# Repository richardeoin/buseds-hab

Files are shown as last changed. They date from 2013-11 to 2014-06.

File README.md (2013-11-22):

TODO: Find a better name for this project than "buseds-hab"!

### [Components List](Components.md)

### [Block Diagram](Block-Diagram.md)

### [Power Budget](power-budget.md)

### Design Notes

The electronics collects data from the sensors and GPS. [Common GPS errors](http://ukhas.org.uk/guides:common_coding_errors_payload_testing).

The data is formatted as a
[UKHAS Telemetry String](http://ukhas.org.uk/communication:protocol)
and transmitted on 434.075MHz using a NTX2
transmitter. [Useful guide to using NTX2](http://ukhas.org.uk/guides:linkingarduinotontx2).
The Telemetry Strings are also logged to a µSD card.

Gets received by Yaesu FT790R.

Audio links to laptop, UKHAS's
[dl-fldigi](http://ukhas.org.uk/projects:dl-fldigi) is used to decode and upload.

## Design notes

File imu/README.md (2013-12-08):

## Firmware for the Sparkfun IMU

I have configured the firmware to output both processed and raw data,
and to do so over the SPI Bus.

### Building

I used the Arduino IDE (Version 1.0.5). You might be able to upload to
the board directly from the IDE, otherwise you need to extract the
intel `.hex` file. In linux it's under
`/tmp/build..../S9DOF_AHRS.cpp.hex`, windows users can find
it in `C:\Users\Owner\AppData\Local\Temp\build...\S9DOF_AHRS.cpp.hex`.

I used
[this](http://mbed.org/users/aberk/notebook/avr910-in-system-programming-using-mbed/)
program for the mBed to actually flash the board. See the
[wiring diagram](SPI_Wire_Connections.pdf).

### Status LED

In SPI mode the Status LED is wired to the SCK signal, so will not work properly!

### Slave Select Pin

The slave select pin is not normally broken out on this board, so this
firmware outputs it on the `TXO` connection. The slave select pin
clocks for each byte, rather than each sentence so that a fully
compliant SPI slave can read every byte.

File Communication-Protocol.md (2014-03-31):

## Communication Protocol for the Payload

* **Callsign**                     BUSEDS1
* **Sentence ID (Increments)**     1
* **Time of Day (from GPS)**       12:14:15
* **GPS Latitude (Decimal Degrees)**  51.234532
* **GPS Longitude (Decimal Degrees)** -2.593403
* **GPS Altitude (Meters)**        114
* **GPS Satillites in View**       7
* **Barometric Altitude (Meters)** 92.3
* **External Temperature (from TMP102)**    18.2
* **Internal Temperature (from Barometer)** 22.1
* **Acceleration X**               100
* **Acceleration Y**               100
* **Acceleration Z**               100
* **Minutes until Cutdown**        120
* **Battery on Cutdown Line**      5.6
* **Checksum**                     XMODEM 16 bit CRC

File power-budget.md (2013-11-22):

## Power Supply

The regualator on the IMU board can supply 3.3V for the Microcontroller, Sensors, SD and Radio. The GPS can use it's own on-board regulator.

Is 4.5V nominal voltage is acceptable? Can the GPS keep going down to about 3.6V with no loss of performance?

## Power Consumption

* Microcontroller - 5mA
* Sensors - 7mA
* GPS - 70mA
* Radio - 18mA
* SD Card - 30mA

* Safety Margin - 20mA

* Total - 150mA

## How Long??

| Battery | Capacity | Operating Time @ 150mA | Price
| --- | --- | --- | ---
| [Energiser AAA](http://uk.farnell.com/energizer/lr03fsb4/battery-aaa-ultra-pk4/dp/3925535) | 1200mAh | 8 Hours | £4.65
| [Energiser AA](http://uk.farnell.com/energizer/lr6-fsb4/battery-aa-ultra-pk4/dp/3925547) | 2900mAh | 19 Hours | £4.70
| [Energiser C](http://uk.farnell.com/energizer/lr14fsb2/battery-c-ultra-pk2/dp/3925559) | 8400mAh | 56 Hours | £9.40

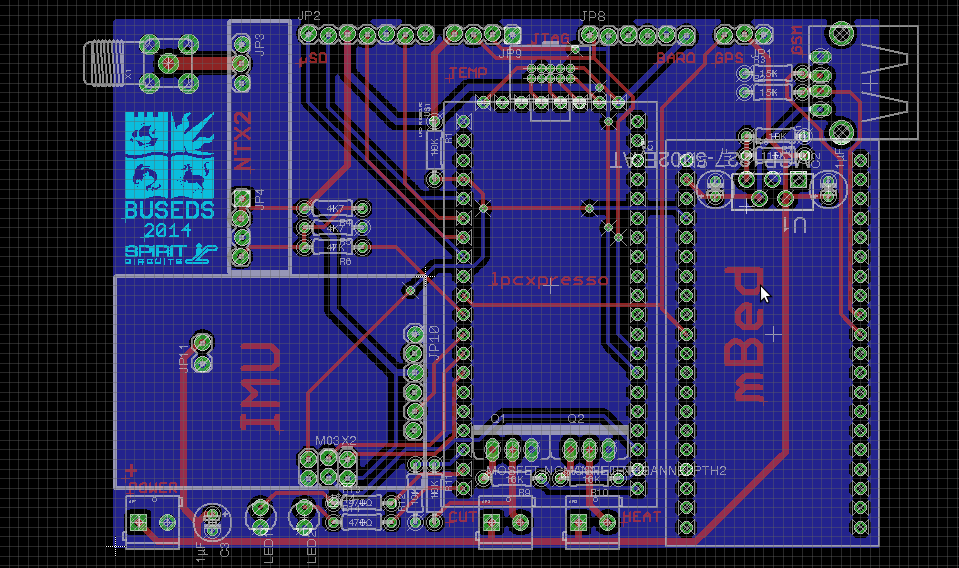
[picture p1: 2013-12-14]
hardware/buseds-hab-board.png

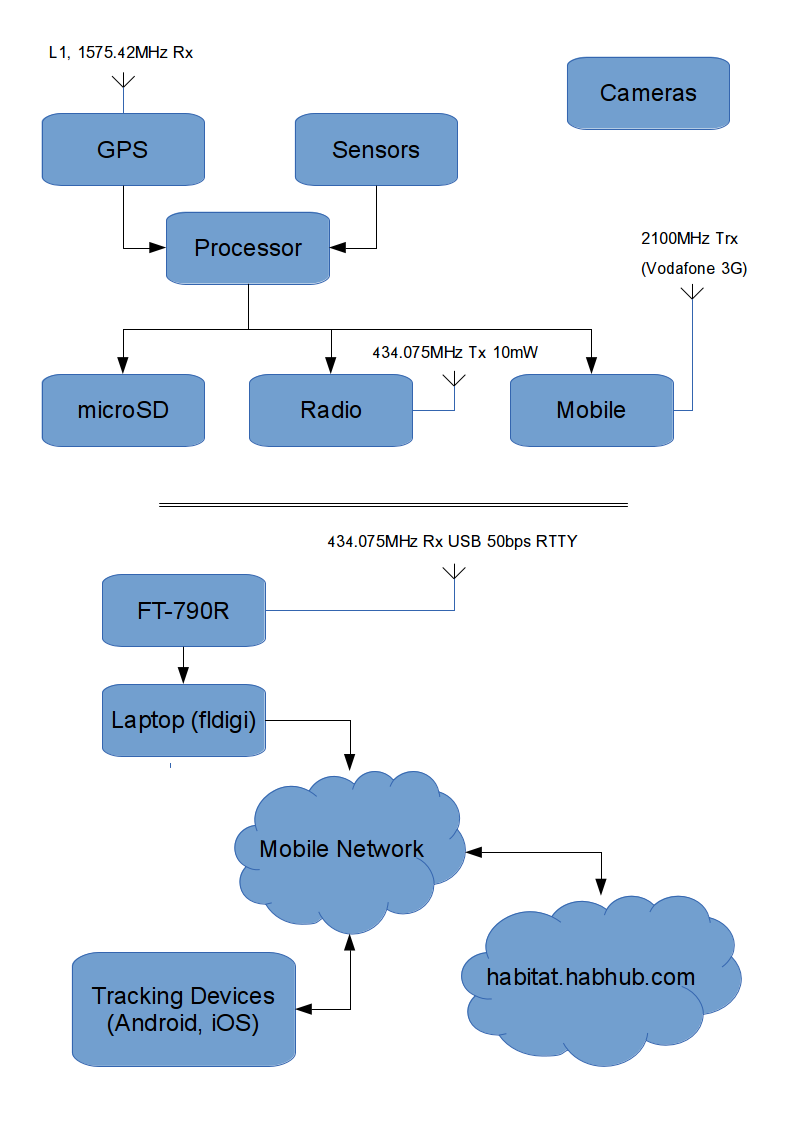
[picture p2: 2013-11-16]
block-diagram.png

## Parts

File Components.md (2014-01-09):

## Component Descriptions

| Component | Part Number | Product Page | Schematic / Datasheet | Bus | Weight | Current Draw (Operational @ 3.3V) | Minimum Operating Temperature | Price
| --- | --- | --- | --- | --- | --- | --- | --- | ---
| Temperature Sensor | TMP102 | [Sparkfun](https://www.sparkfun.com/products/9418) | [TI](https://www.sparkfun.com/datasheets/Sensors/Temperature/tmp102.pdf) | I2C 0x90 - 0x96 | | 10µA | -55°C
| Pressure Sensor | BMP085 | [Sparkfun](https://www.sparkfun.com/products/retired/9694) [Replacement, Generic Breakout](http://www.ebay.co.uk/itm/BMP085-Breakout-Barometric-Pressure-Sensor-/321123029556) | [Bosch](http://dlnmh9ip6v2uc.cloudfront.net/datasheets/Sensors/Pressure/BST-BMP085-DS000-06.pdf) | I2C 0xEE || 10µA | -40°C (0°C for full accuracy)
| IMU | SEN-10736 | [Sparkfun](https://www.sparkfun.com/products/10736) | [Sparkfun](http://dlnmh9ip6v2uc.cloudfront.net/datasheets/Sensors/IMU/9DOF-Razor-v22.pdf) |
| Accelerometer | ADXL345 | [Sparkfun] (https://www.sparkfun.com/products/9045) | [Analog Devices] (https://www.sparkfun.com/datasheets/Sensors/Accelerometer/ADXL345.pdf) | I2C 0x1D || 40µA @ 2.5V | -40°C
| Gyroscope | ITG-3200 | [Sparkfun] (https://www.sparkfun.com/products/9793) | [InvenSense] (https://www.sparkfun.com/datasheets/Sensors/Gyro/PS-ITG-3200-00-01.4.pdf) | I2C 0xD0 - 0xD2 || 6.5mA @ 2.5V | -40°C
| Magnetometer | HMC5883L | [Sparkfun] (https://www.sparkfun.com/products/10494) | [Honeywell] (http://dlnmh9ip6v2uc.cloudfront.net/datasheets/Sensors/Magneto/HMC5883L-FDS.pdf) | I2C 0x3C || 100μA @ 2.5V | -30°C
| IMU Processor | ATMega 328P |
| GPS | EM406 | [Sparkfun] (https://www.sparkfun.com/products/465) | [GlobalSat] (https://www.sparkfun.com/datasheets/GPS/EM-406A_User_Manual.PDF) | Serial 8N1 4800 || 70mA @ 4.5-6.5V | -40°C
| Radio | NTX2 | [Radiomatrix] (http://www.radiometrix.com/content/ntx2) | [Radiomatrix] (http://www.radiometrix.com/files/additional/ntx2nrx2.pdf) | Serial RTTY 8N2 50 / 300 || 18mA | -10°C (Will drift anyhow)
| SD Card | | | | SPI 1MHz || 30mA |
| SD Card Holder | | [Proto PIC](http://proto-pic.co.uk/breakout-board-for-microsd-transflash/) | | | | | | £4.59
| mBed || [mBed](mbed.org) | | | | [100mA](http://mbed.org/users/no2chem/notebook/mbed-power-controlconsumption/) |
| LPC1115 | LPC1115 | [Farnell](http://uk.farnell.com/nxp/om13035/lpc1115-lpcxpresso-eval-board/dp/2103787) | [Schematic](http://www.embeddedartists.com/sites/default/files/docs/schematics/LPCXpressoLPC1114revA.pdf) [Datasheet](http://www.nxp.com/documents/data_sheet/LPC111X.pdf) | | | 5mA @ 24MHz | -40°C | £15.15
| Battery Connectors | SPH-004T-P0.5S, PHR-2 | [Contact](http://uk.farnell.com/jsp/search/productdetail.jsp?SKU=1830762) [Housing](http://uk.farnell.com/jsp/search/productdetail.jsp?SKU=3616186) | | | | | | £0.56

## Minor Components

| ID | Part Number | Description | Supplier | Order Code | Quantity
| --- | --- | --- | --- | --- | ---
| U1 | MCP1827 | ADJ VREG 1.5A | Farnell | [1840847](http://uk.farnell.com/jsp/search/productdetail.jsp?id=1840847) | 1
| C1, C2 | | 1µF Capacitor, 16V, 5mm | Farnell | [1236655](http://uk.farnell.com/jsp/search/productdetail.jsp?id=1236655) | 2
| Q1, Q2 | PSMN2R7-30PL | MOSFET,N CH,30V,100A,TO-220 | Farnell | [1845665](http://uk.farnell.com/jsp/search/productdetail.jsp?id=1845665) | 2
| JP5, JP6, JP7 | CTB3051/2BK | TERMINAL BLOCK, PCB, 3.5MM, 2WAY | Farnell | [3882615](http://uk.farnell.com/jsp/search/productdetail.jsp?id=3882615) | 3
| LED1 | | LED, ORANGE, 3MM, 50MCD, 629NM | Farnell | [2112099](http://uk.farnell.com/jsp/search/productdetail.jsp?id=2112099) | 1
| LED2 | | LED, GREEN, 3MM, 50MCD, 572NM | Farnell | [2112096](http://uk.farnell.com/jsp/search/productdetail.jsp?id=2112096) | 1
| JTAG1 | | HEADER, VERTICAL, 2ROW, 10WAY | Farnell | [1022305](http://uk.farnell.com/jsp/search/productdetail.jsp?id=1022305) | 1
| R1, R7, R9 - R12 | | 10kΩ Resistor, 0.25W | Generic | | 6
| R2, R3 | | 15kΩ Resistor, 0.25W | Generic | | 2
| R4, R5 | | 4.7kΩ Resistor, 0.25W | Generic | | 2
| R6 | | 47kΩ Resistor, 0.25W | Generic | | 1
| R8 | | 115kΩ Resistor, 0.25W, 1% | Farnell | [2329996](http://uk.farnell.com/jsp/search/productdetail.jsp?id=2329996) | 1
| R13, R14 | | 470Ω Resistor | Generic | 2
| X1 | 5-1814832-1 | SMA Socket, Straight Vertical, PCB Mount, 50Ω | Farnell | [1248990](http://uk.farnell.com/jsp/search/productdetail.jsp?id=1248990) | 1
| Various | M20-7822046 | CONNECTOR, RECEPTACLE, THT, 2.54MM, 20P | Farnell | [7991967](http://uk.farnell.com/jsp/search/productdetail.jsp?id=7991967) | 4

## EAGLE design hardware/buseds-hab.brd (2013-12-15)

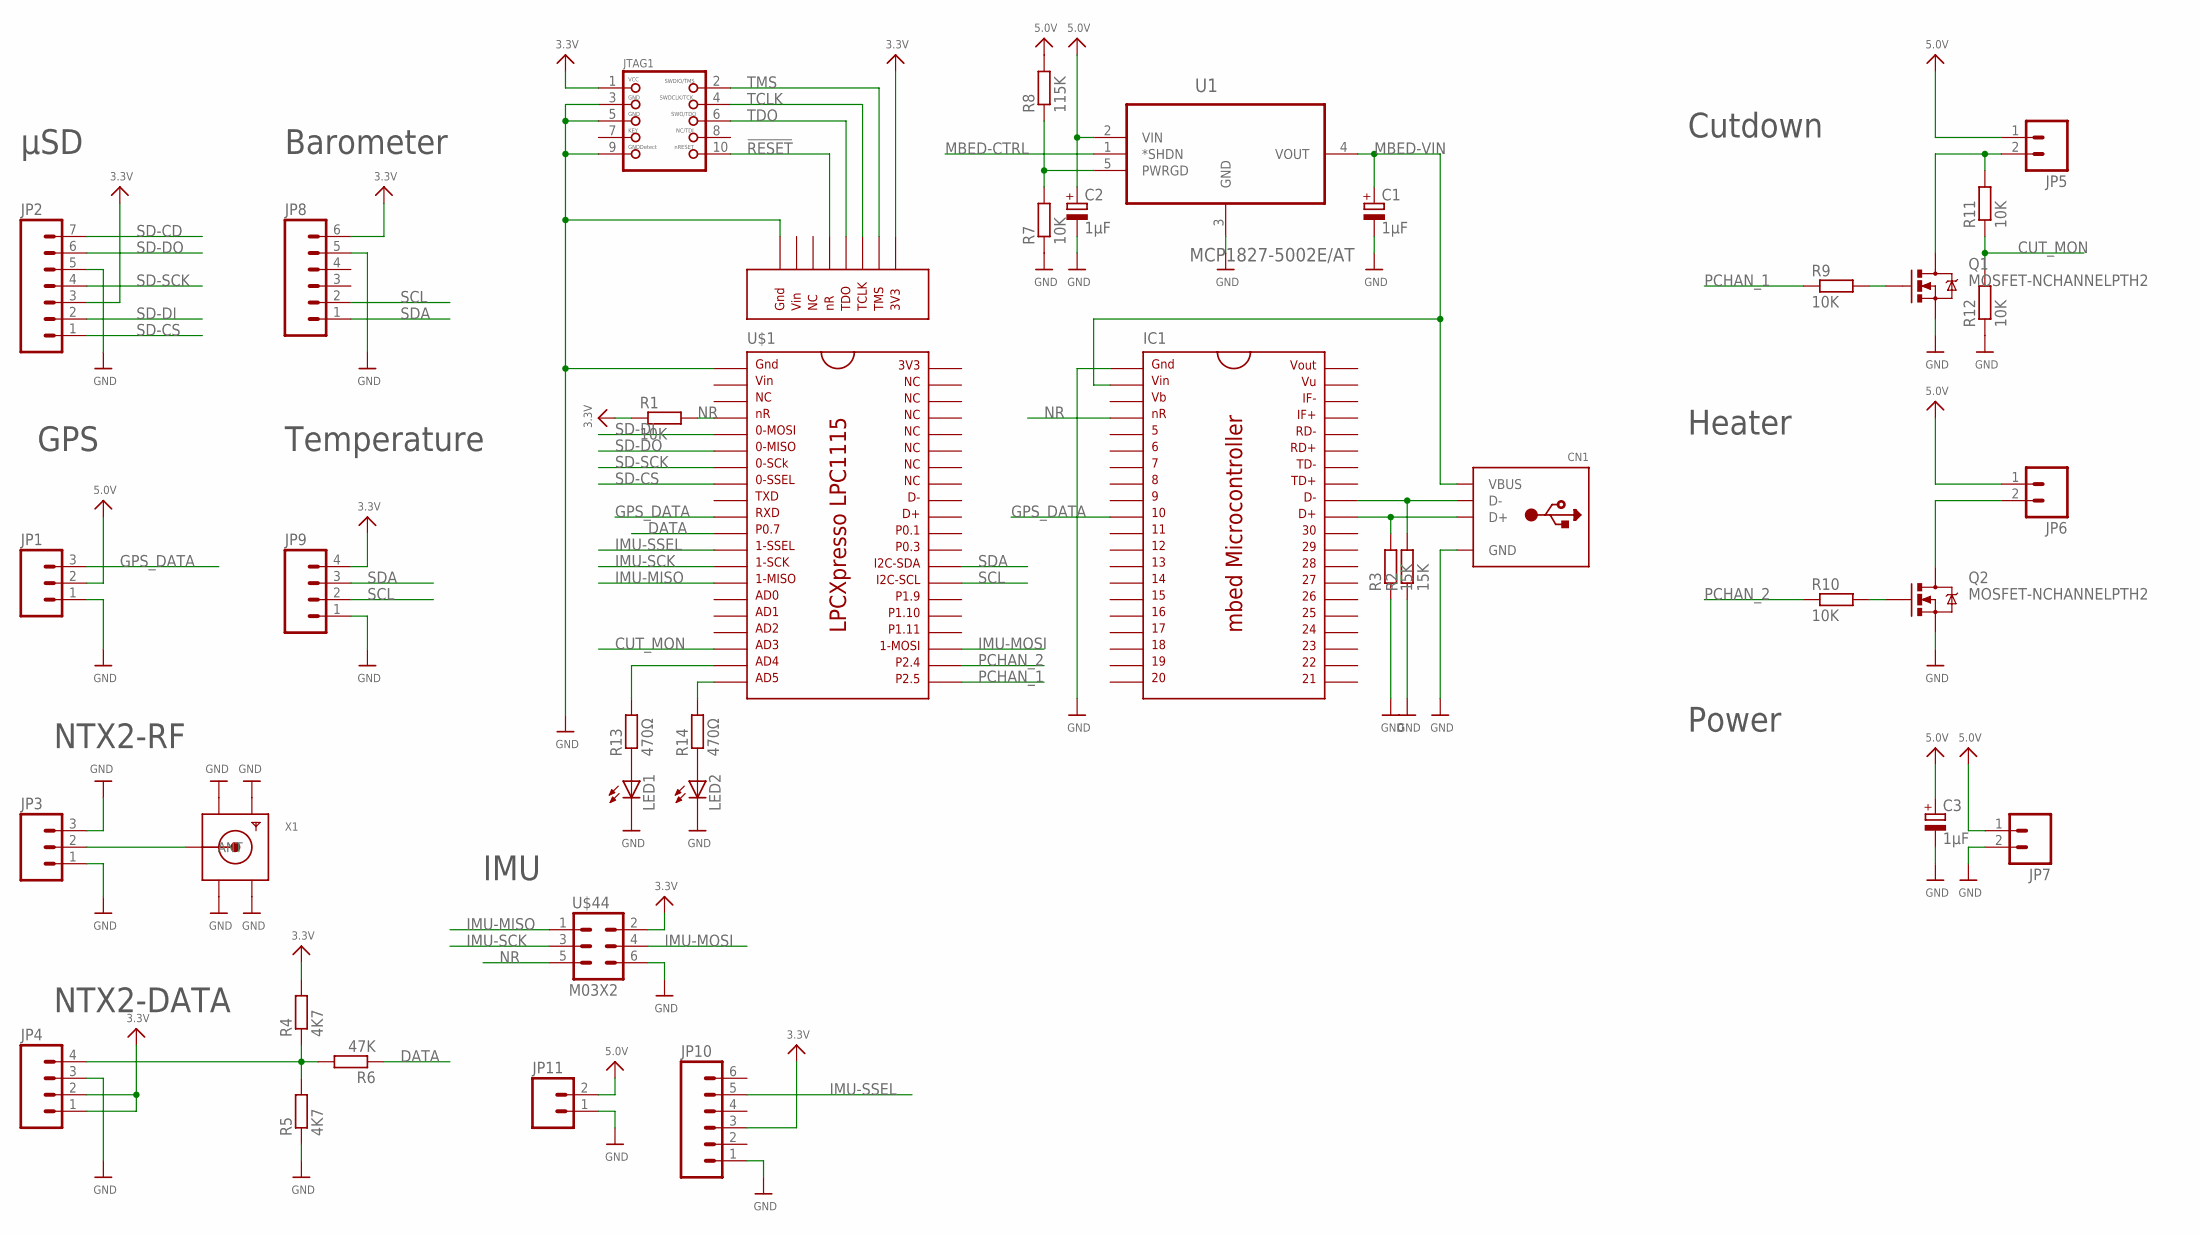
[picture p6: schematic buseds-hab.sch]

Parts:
C1, C2, C3: 1µF; E2-5
CN1: USB_TYPEAPTHFML; USB_HOST-PTH
IC1: MBED; DIL40_0.9
JP1, JP3: M03LOCK; 1X03_LOCK
JP2: M07LOCK; 1X07_LOCK
JP4, JP9: M04LOCK; 1X04_LOCK
JP5, JP6, JP7: M023.5MM_LOCK; SCREWTERMINAL-3.5MM-2_LOCK
JP8, JP10: M06LOCK; 1X06_LOCK
JP11: M02LOCK; 1X02_LOCK
JTAG1: JTAG-CORTEXM3; 2X05_1.27MM
LED1, LED2: LED3MM
Q1, Q2: MOSFET-NCHANNELPTH2; TO220V
R1, R7, R9, R10, R11, R12: 10K; 0204/7
R2, R3: 15K; 0204/7
R4, R5: 4K7; 0204/7
R6: 47K; 0204/7
R8: 115K; 0204/7
R13, R14: 470Ω; 0204/7
U1: MCP1827-5002E/AT; TO170P482X1024X3124-5P
U$1: LPCXPRESSOLPC; LPCXPRESSO
U$44: M03X2; 2X3_LOCK
X1: SMACONNECTOR; SMA90_DIP

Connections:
3.3V: JP2.3, JP4.1, JP4.2, JP8.6, JP9.4, JP10.3, JTAG1.1, R1.1, R4.2, U$1.P-1, U$44.2
5.0V: C2.+, C3.+, JP1.2, JP5.1, JP6.1, JP7.1, JP11.2, R8.2, U1.2 (VIN)
!RESET!: JTAG1.10, U$1.P-5
CUT_MON: R11.1, R12.2, U$1.18
D+: CN1.D+, IC1.31, R3.2
D-: CN1.D-, IC1.32, R2.2
DATA: R6.1, U$1.11
GND: C1.-, C2.-, C3.-, CN1.GND, IC1.1, JP1.1, JP2.5, JP3.1, JP3.3, JP4.3, JP7.2, JP8.5, JP9.1, JP10.1, JP11.1, JTAG1.3, JTAG1.5, JTAG1.9, LED1.K (C), LED2.K (C), Q1.3 (S), Q2.3 (S), R2.1, R3.1, R5.1, R7.1, R12.1, U1.3 (GND), U$1.1, U$1.P-8, U$44.6, X1.GND1, X1.GND2, X1.GND3, X1.GND4
GPS_DATA: IC1.10, JP1.3, U$1.10
IMU-MISO: U$1.14, U$44.1
IMU-MOSI: U$1.23, U$44.4
IMU-SCK: U$1.13, U$44.3
IMU-SSEL: JP10.5, U$1.12
MBED-CTRL: U1.1 (*SHDN)
MBED-VIN: C1.+, CN1.VBUS, IC1.2, U1.4 (VOUT)
unnamed: R7.2, R8.1, U1.5 (PWRGD)
unnamed: LED1.A, R13.1
unnamed: LED2.A, R14.1
unnamed: R14.2, U$1.20
unnamed: R13.2, U$1.19
NR: IC1.4, R1.2, U$1.4, U$44.5
PCHAN_1: R9.1, U$1.21
PCHAN_1_G: Q1.1 (G), R9.2
PCHAN_1_S: JP5.2, Q1.2 (D), R11.2
PCHAN_2: R10.1, U$1.22
PCHAN_2_G: Q2.1 (G), R10.2
PCHAN_2_S: JP6.2, Q2.2 (D)
RF: JP3.2, X1.ANTENNA (ANT)
RF-DATA: JP4.4, R4.1, R5.2, R6.2
SCL: JP8.2, JP9.2, U$1.27
SD-CD: JP2.7
SD-CS: JP2.1, U$1.8
SD-DI: JP2.2, U$1.5
SD-DO: JP2.6, U$1.6
SD-SCK: JP2.4, U$1.7
SDA: JP8.1, JP9.3, U$1.28
TCLK: JTAG1.4, U$1.P-3
TDO: JTAG1.6, U$1.P-4
TMS: JTAG1.2, U$1.P-2

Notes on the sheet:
µSD
GPS
NTX2-RF
NTX2-DATA
Temperature
Barometer
Cutdown
Heater
Power
IMU

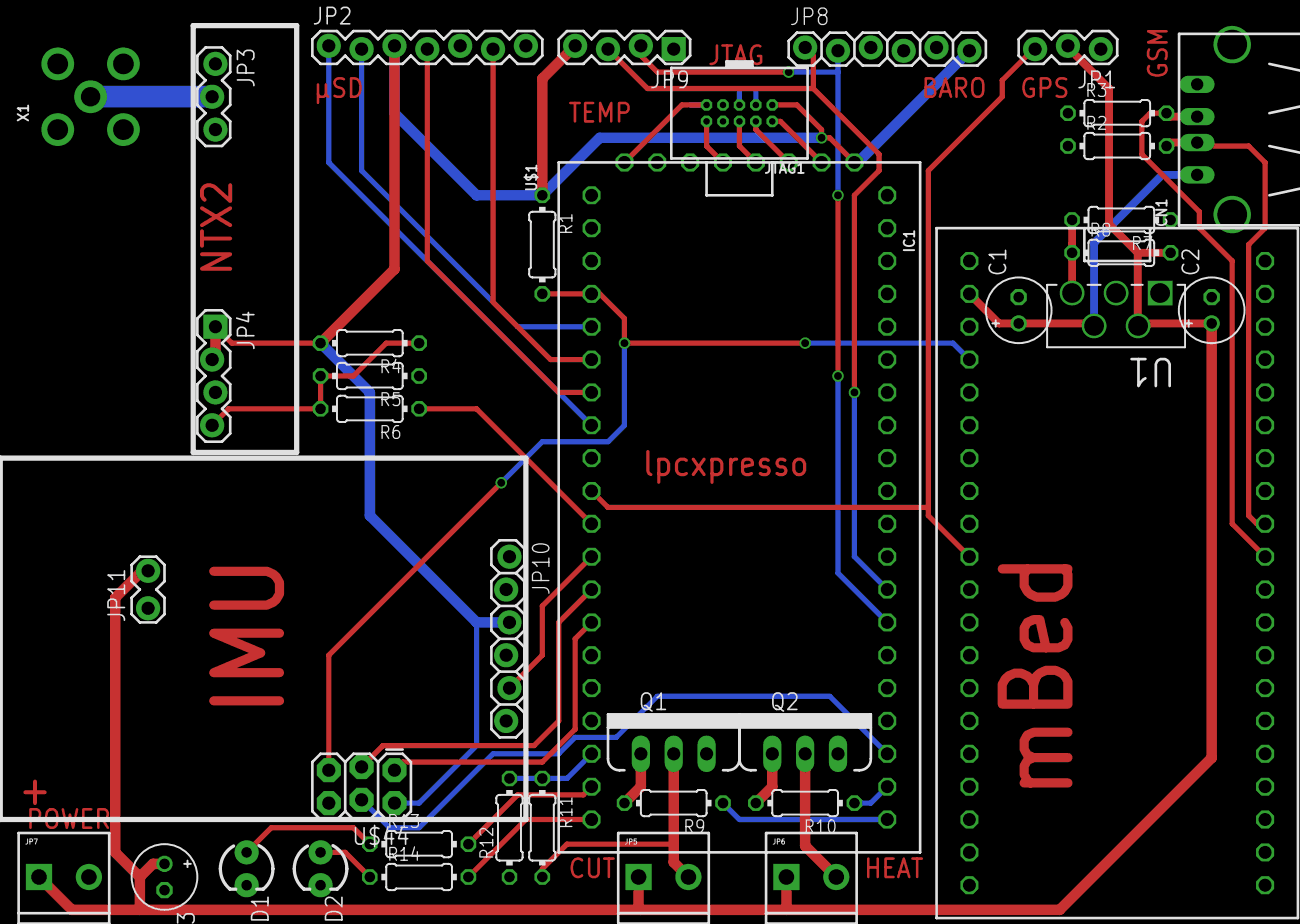
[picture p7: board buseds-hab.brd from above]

Board: 2 copper layers, 39 parts (0 on the bottom side), 37 nets.

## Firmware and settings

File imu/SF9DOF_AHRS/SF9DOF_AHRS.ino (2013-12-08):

// Sparkfveun 9DOF Razor IMU AHRS
// 9 Degree of Measurement Attitude and Heading Reference System
// Firmware v1.0
//
// Released under Creative Commons License 
// Code by Doug Weibel and Jose Julio
// Based on ArduIMU v1.5 by Jordi Munoz and William Premerlani, Jose Julio and Doug Weibel

// Axis definition: 
   // X axis pointing forward (to the FTDI connector)
   // Y axis pointing to the right 
   // and Z axis pointing down.
// Positive pitch : nose up
// Positive roll : right wing down
// Positive yaw : clockwise

/* Hardware version - v13
	
	ATMega328@3.3V w/ external 8MHz resonator
	High Fuse DA
        Low Fuse FF
	
	ADXL345: Accelerometer
	HMC5843: Magnetometer
	LY530:	Yaw Gyro
	LPR530:	Pitch and Roll Gyro

        Programmer : 3.3v FTDI
        Arduino IDE : Select board  "Arduino Duemilanove w/ATmega328"
*/
// This code works also on ATMega168 Hardware

#include <Wire.h>
#include <SPI.h>
#include "pins_arduino.h"

// ADXL345 Sensitivity(from datasheet) => 4mg/LSB   1G => 1000mg/4mg = 256 steps
// Tested value : 248
#define GRAVITY 248  //this equivalent to 1G in the raw data coming from the accelerometer 
#define Accel_Scale(x) x*(GRAVITY/9.81)//Scaling the raw data of the accel to actual acceleration in meters for seconds square

#define ToRad(x) (x*0.01745329252)  // *pi/180
#define ToDeg(x) (x*57.2957795131)  // *180/pi

// LPR530 & LY530 Sensitivity (from datasheet) => (3.3mv at 3v)at 3.3v: 3mV/º/s, 3.22mV/ADC step => 0.93
// Tested values : 0.92
#define Gyro_Gain_X 0.92 //X axis Gyro gain
#define Gyro_Gain_Y 0.92 //Y axis Gyro gain
#define Gyro_Gain_Z 0.92 //Z axis Gyro gain
#define Gyro_Scaled_X(x) x*ToRad(Gyro_Gain_X) //Return the scaled ADC raw data of the gyro in radians for second
#define Gyro_Scaled_Y(x) x*ToRad(Gyro_Gain_Y) //Return the scaled ADC raw data of the gyro in radians for second
#define Gyro_Scaled_Z(x) x*ToRad(Gyro_Gain_Z) //Return the scaled ADC raw data of the gyro in radians for second

#define Kp_ROLLPITCH 0.02
#define Ki_ROLLPITCH 0.00002
#define Kp_YAW 1.2
#define Ki_YAW 0.00002

/*For debugging purposes*/
//OUTPUTMODE=1 will print the corrected data, 
//OUTPUTMODE=0 will print uncorrected data of the gyros (with drift)
#define OUTPUTMODE 1

//#define PRINT_DCM 0     //Will print the whole direction cosine matrix
#define PRINT_ANALOGS 1 //Will print the analog raw data
#define PRINT_EULER 1   //Will print the Euler angles Roll, Pitch and Yaw
#define ENABLE_SPI 1  // Enable SPI Master - Disable Serial

#define ADC_WARM_CYCLES 50
#define STATUS_LED 13 
#define SS_OUTPUT 12  // We re-purpose the MISO pin

int8_t sensors[3] = {1,2,0};  // Map the ADC channels gyro_x, gyro_y, gyro_z
int SENSOR_SIGN[9] = {-1,1,-1,1,1,1,-1,-1,-1};  //Correct directions x,y,z - gyros, accels, magnetormeter

float G_Dt=0.02;    // Integration time (DCM algorithm)  We will run the integration loop at 50Hz if possible

long timer=0;   //general purpuse timer
long timer_old;
long timer24=0; //Second timer used to print values 
int AN[6]; //array that store the 3 ADC filtered data (gyros)
int AN_OFFSET[6]={0,0,0,0,0,0}; //Array that stores the Offset of the sensors
int ACC[3];          //array that store the accelerometers data

int accel_x;
int accel_y;
int accel_z;
int magnetom_x;
int magnetom_y;
int magnetom_z;
float MAG_Heading;

float Accel_Vector[3]= {0,0,0}; //Store the acceleration in a vector
float Gyro_Vector[3]= {0,0,0};//Store the gyros turn rate in a vector
float Omega_Vector[3]= {0,0,0}; //Corrected Gyro_Vector data
float Omega_P[3]= {0,0,0};//Omega Proportional correction
float Omega_I[3]= {0,0,0};//Omega Integrator
float Omega[3]= {0,0,0};

// Euler angles
float roll;
float pitch;
float yaw;

float errorRollPitch[3]= {0,0,0}; 
float errorYaw[3]= {0,0,0};

unsigned int counter=0;
byte gyro_sat=0;

float DCM_Matrix[3][3]= {
  {
    1,0,0  }
  ,{
    0,1,0  }
  ,{
    0,0,1  }
}; 
float Update_Matrix[3][3]={{0,1,2},{3,4,5},{6,7,8}}; //Gyros here


float Temporary_Matrix[3][3]={
  {
    0,0,0  }
  ,{
    0,0,0  }
  ,{
    0,0,0  }
};
 
//ADC variables
volatile uint8_t MuxSel=0;
volatile uint8_t analog_reference;
volatile uint16_t analog_buffer[8];
volatile uint8_t analog_count[8];

void setup()
{
#if ENABLE_SPI == 0
  Serial.begin(57600);
#endif
  pinMode (STATUS_LED,OUTPUT);  // Status LED

#if ENABLE_SPI == 1
  pinMode (1,OUTPUT); 
  pinMode (SS,OUTPUT); 
  digitalWrite(1, HIGH);  // ensure SS stays high for now
  digitalWrite(SS, HIGH);  // ensure SS stays high for now
  // start the SPI library:
  SPI.begin();
  // Slow down the master a bit
  SPI.setClockDivider(SPI_CLOCK_DIV8);
#endif
 
  Analog_Reference(DEFAULT); 
  Analog_Init();
  I2C_Init();
  Accel_Init();
  Read_Accel();

#if ENABLE_SPI == 1
  spi_transfer_str("Sparkfun 9DOF Razor AHRS");
  spi_println();
#else
  Serial.println("Sparkfun 9DOF Razor AHRS");
#endif

  digitalWrite(STATUS_LED,LOW);
  delay(1500);
 
  // Magnetometer initialization
  Compass_Init();
  
  // Initialze ADC readings and buffers
  Read_adc_raw();
  delay(20);
  
  for(int i=0;i<32;i++)    // We take some readings...
    {
    Read_adc_raw();
    Read_Accel();
    for(int y=0; y<6; y++)   // Cumulate values
      AN_OFFSET[y] += AN[y];
    delay(20);
    }
    
  for(int y=0; y<6; y++)
    AN_OFFSET[y] = AN_OFFSET[y]/32;
    
  AN_OFFSET[5]-=GRAVITY*SENSOR_SIGN[5];

  //Serial.println("Offset:");
  for(int y=0; y<6; y++) {
#if ENABLE_SPI == 1
  spi_transfer_int(AN_OFFSET[y]);
  spi_println();
#else
  Serial.println(AN_OFFSET[y]);
#endif
  }
  delay(2000);
  digitalWrite(STATUS_LED,HIGH);
    
  Read_adc_raw();     // ADC initialization
  timer=millis();
  delay(20);
  counter=0;
}

void loop() //Main Loop
{

#if ENABLE_SPI == 1
  // enable Slave Select
  //digitalWrite(SS, LOW);    // SS is pin 10
#endif 
  
  if((millis()-timer)>=20)  // Main loop runs at 50Hz
  {
    counter++;
    timer_old = timer;
    timer=millis();
    if (timer>timer_old)
      G_Dt = (timer-timer_old)/1000.0;    // Real time of loop run. We use this on the DCM algorithm (gyro integration time)
    else
      G_Dt = 0;
    
    // *** DCM algorithm
    // Data adquisition
    Read_adc_raw();   // This read gyro data
    Read_Accel();     // Read I2C accelerometer
    
    if (counter > 5)  // Read compass data at 10Hz... (5 loop runs)
      {
      counter=0;
      Read_Compass();    // Read I2C magnetometer
      Compass_Heading(); // Calculate magnetic heading  
      }
    
    // Calculations...
    Matrix_update(); 
    Normalize();
    Drift_correction();
    Euler_angles();
    // ***

#if ENABLE_SPI == 1
    spi_printdata();
#else
    printdata();
#endif
    
    //Turn off the LED when you saturate any of the gyros.
    if((abs(Gyro_Vector[0])>=ToRad(300))||(abs(Gyro_Vector[1])>=ToRad(300))||(abs(Gyro_Vector[2])>=ToRad(300)))
      {
      if (gyro_sat<50)
        gyro_sat+=10;
      }
    else
      {
      if (gyro_sat>0)
        gyro_sat--;
      }
  
    if (gyro_sat>0)
      digitalWrite(STATUS_LED,LOW);  
    else
      digitalWrite(STATUS_LED,HIGH);  
  
  }

#if ENABLE_SPI == 1
  // disable Slave Select
  //digitalWrite(SS, HIGH);
#endif 
   
}

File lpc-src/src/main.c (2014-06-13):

/*
 * Demo C Application: Toggles an output at 20Hz.
 * Copyright (C) 2013  Richard Meadows
 *
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
 * THE SOFTWARE IS PROVIDED "AS IS", WITHOUT WARRANTY OF ANY KIND,
 * EXPRESS OR IMPLIED, INCLUDING BUT NOT LIMITED TO THE WARRANTIES OF
 * MERCHANTABILITY, FITNESS FOR A PARTICULAR PURPOSE AND
 * NONINFRINGEMENT. IN NO EVENT SHALL THE AUTHORS OR COPYRIGHT HOLDERS BE
 * LIABLE FOR ANY CLAIM, DAMAGES OR OTHER LIABILITY, WHETHER IN AN ACTION
 * OF CONTRACT, TORT OR OTHERWISE, ARISING FROM, OUT OF OR IN CONNECTION
 * WITH THE SOFTWARE OR THE USE OR OTHER DEALINGS IN THE SOFTWARE.
 */

#include "LPC11xx.h"
#include "rtty.h"
#include "i2c.h"
#include "tmp102.h"
#include "imu.h"
#include "spi.h"
#include "leds.h"
#include "bmp085.h"
#include "altitude.h"
#include "cutdown_heat.h"
#include "mbed.h"
#include "sd.h"
#include "sd_spi.h"
#include "wdt.h"
#include "gps.h"
#include "uart.h"
#include "protocol.h"
#include "disk_write.h"
#include "pwrmon.h"

/**
saydah **************************
 Flight Parameters
 *************************/

/**
 * Watchdog disabled to allow debugging - REMOVE BEFORE FLIGHT
 */
/*#define WATCHDOG_DISABLED*/
/**
 * The number of minutes until the cutdown system activates
 * MAX = 2^32/60*RTTY_BAUD ~= 10^6
 */
#define CUTDOWN_TIME		180
/**
 * The mBed is powered on below the given barometric altitude in
 * meters
 */
#define GSM_ON_BELOW_ALTITUDE	1000
/**
 * The altitude ceiling at which cutdown will occour (in meters)
 */
#define CUTDOWN_CEILING		40000
/**
 * The minimum barometric altitude in meters at which the balloon must
 * be for cutdown to occour.
 */
#define MIN_CUTDOWN_ALTITUDE	1000
/**
 * The threshold temperature for the heater to activate in °C
 */
#define HEATER_THRESHOLD	-30



/**
 **************************
 System Parameters
 *************************/

/**
 * RTTY Baud Clock.
 */
#define RTTY_BAUD       	50
/**
 * The maximum length of a single transmitter string
 */
#define TX_STRING_LENGTH	0x200

/**
 **************************
 Globals
 *************************/

int sd_good = 0;
uint32_t ticks_until_cutdown = CUTDOWN_TIME * RTTY_BAUD * 60;
float cutdown_voltage = 0;

/**
 **************************
 System Control Logic
 *************************/

void control_gsm(double altitude) {
  if (altitude < GSM_ON_BELOW_ALTITUDE && altitude != -1) {
    MBED_ON();
  } else {
    MBED_OFF();
  }
}
void control_cutdown(uint32_t ticks, double altitude) {
  if ((ticks == 0 && altitude > MIN_CUTDOWN_ALTITUDE) ||
      (altitude > CUTDOWN_CEILING && altitude != -1)) {

    CUTDOWN_ON(); // Mechanical disconnect
  } else {
    CUTDOWN_OFF();
  }
}
void control_heater(double internal_temperature) {
  if (internal_temperature < HEATER_THRESHOLD && internal_temperature != -1) {
    HEATER_ON();
  } else {
    HEATER_OFF();
  }
}

/**
 * Called at the end of an ADC conversion
 */
void pwrmon_callback(uint16_t adc_value) {
  cutdown_voltage = adc_value * (6.6 / 1024);
}

/**
 * Main system entry point
 */
int main (void) {
  SystemInit();

  /* Initialise Pins */
  CUTDOWN_OFF();
  HEATER_OFF();
  MBED_OFF();
  GREEN_OFF();

  /* Update the value of SystemCoreClock */
  SystemCoreClockUpdate();

  /* Initialise Interfaces */
  i2c_init();
  spi_init(process_imu_frame); // IMU
  sd_spi_init(); // SD
  uart_init(); // GPS
  pwrmon_init(); // ADC

  /* Initialise Sensors */
  init_barometer();

  /* SD Card */
  if (initialise_card()) { // Initialised to something
    if (disk_initialize() == 0) { // Disk initialisation was successful
      sd_good = 1;
    }
  }

  GREEN_ON();

  /* Configure the SysTick */
  NVIC_SetPriority(SysTick_IRQn, 0); // Highest Priority Interrupt
  SysTick_Config(SystemCoreClock / RTTY_BAUD);

  /* Watchdog - Disabled for debugging */
#ifndef WATCHDOG_DISABLED
  init_watchdog();
#endif

  struct barometer* b;
  struct imu_raw ir;
  struct gps_data gd;
  struct gps_time gt;
  double alt, ext_temp;
  int tx_length; // The length of the built tx string

  char tx_string[TX_STRING_LENGTH];

  while (1) {
    /* Grab Data */
    pwrmon_start(pwrmon_callback);
    b = get_barometer();
    get_imu_raw_data(&ir);
    get_gps_data(&gd);
    get_gps_time(&gt);
    ext_temp = get_temperature();

    /* Data Processing */
    if (b->valid) {
      alt = pressure_to_altitude(b->pressure);
    } else {
      alt = -1;
      b->temperature = -1;
    }

    /* Act on the data */
    control_gsm(alt);
    control_cutdown(ticks_until_cutdown, alt);
    control_heater(b->temperature);

    /* Create a protocol string */
    int cutstat;
    if (ticks_until_cutdown == 0) {
      cutstat = -1;
    } else {
      cutstat = ticks_until_cutdown / (RTTY_BAUD*60);
    }
    tx_length = build_communications_frame(tx_string, TX_STRING_LENGTH,
					   &gt, b, &gd, alt, ext_temp, &ir,
					   cutstat,  cutdown_voltage);

    /* Transmit - Quietly fails if another transmission is ongoing */
    rtty_set_string(tx_string, tx_length);

    /* Store */
    if (sd_good) {
      tx_length -= 2; // Remove \n\0
      tx_length += communications_frame_add_extra(tx_string + tx_length,
				     TX_STRING_LENGTH - tx_length, &ir);

      disk_write_next_block((uint8_t*)tx_string, tx_length+1); // Include null terminator
    }

    /* Housekeeping */
    GREEN_TOGGLE();
    feed_watchdog();
  }
}

extern void SysTick_Handler(void) {
  /* Push RTTY bits */
  rtty_tick();
  /* Countdown */
  if (ticks_until_cutdown) {
    ticks_until_cutdown--;
  }
}

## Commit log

2013-11-15 Added a couple more items to components table
2013-11-17 added more information for some components
    updated information on IMU and subcomponents + GPS + Radio
2013-11-17 Added correct part number and schematic link for IMU
2013-11-22 Added to IMU component descriptions
2013-11-22 Added power budget
2013-11-22 Added battery connector
2013-11-22 Adapted makefile for use with blackmagic debug probe on linux
2013-11-22 Added pin usage notes
2013-11-23 Fixed temperature sensor bus address
2013-11-23 Added I2C libraries
2013-11-23 Added temperature sensor support
2013-12-08 Implemented SPI slave for receiving IMU data
2013-12-08 Fixed description on SPI header
2013-12-08 Added code to process IMU data
2013-12-08 Added IMU firmware
2013-12-14 Added replacement pressure sensor
2013-12-14 Started minor parts list for things that will be soldered to the main PCB
2013-12-14 Initial revision of hardware
    [buseds-hab.brd, buseds-hab.sch]
2013-12-14 Cropped board image
2013-12-14 Added JTAG connector
2013-12-15 Made space for voltage regulator tab
    [buseds-hab.brd]
2014-01-04 Added resistors to minor components list
2014-01-04 Added connectors to minor components list
2014-01-09 Corrected JTAG1 connector to something more suitable
2014-01-27 Made basic updates for the new board
2014-01-28 Added header with LED macros
2014-01-28 Only use Green LED for the moment, Yellow LED overrides SWDIO
2014-02-21 Whitespace things, accessor functions for imu, added test build for GPS code
2014-02-26 Initial implementation of uart for the gps
2014-02-26 Added macros for SD CS pin, fixed warnings
    [sd.c]
2014-03-18 Added timeout on transactions to prevent an infinite wait
    [i2c.c]
2014-03-18 Don't use the Yellow LED as it interferes with the programming interface
2014-03-18 Fixed pins for cutdown and heat
2014-03-18 main.c updated for cutdown / heat and SD card
2014-03-21 Initial implementation of watchdog timer
2014-03-21 Rebuild sources.mk, fixed compiler errors on new sources
    [uart.c]
2014-03-22 Added disk write interface which keeps track of the current block
2014-03-28 Implemented cutdown timer
2014-03-31 Modified protocol for cutdown timer
2014-03-31 Added cutdown voltage to the protocol. TODO: Measurement code
2014-03-31 Use current time during protocol test, cutdown voltage to 1dp
2014-03-31 Updates printing to only use formats available in nano.specs, reduceds resource load and hardfaults on processor
2014-03-31 Fixed float printing functions with working versions from UKHAS
2014-04-01 Tidied up main.c, added control logic for heater
2014-04-01 Fixed rounding edge case
2014-04-01 Added cutdown voltage monitoring
2014-04-05 Set interrupt priorities: 1st SysTick, 2nd Everything Else, 3rd Power Mon
2014-04-05 Improve i2c timeouts
2014-04-05 Added preprocessor switch to enable watchdog
2014-04-05 Fixed sd read/write block size
    [sd.c]
2014-06-13 Verify checksums on GPS frames.
    Observed an error in the GPS frame reception (out of order characters) during testing.
    [uart.c]

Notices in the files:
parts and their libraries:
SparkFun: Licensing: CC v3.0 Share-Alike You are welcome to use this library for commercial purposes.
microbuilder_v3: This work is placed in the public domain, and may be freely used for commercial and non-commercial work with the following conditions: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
